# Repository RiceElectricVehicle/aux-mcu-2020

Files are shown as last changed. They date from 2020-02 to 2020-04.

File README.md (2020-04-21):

# Central Controller Code

Initial Author: Boyuan Deng

## Overview

This library is built for Rice Electric Vehicle Electric Team's auxilary board (aux board). The main function of the auxilary board include the following:

1. Take in and respond to information from pedal and break
2. Communicate with and respond to motor controller
3. Enable lighting control through switches installed on board
4. Display the car's status on screen

All the functions mentioned above requires the microcontroller on aux board. We've chosen Teensy 3.5 as the microcontroller, and the language for it is Arduino language, which is essentially C++ with Arduino's special libraries. We chose Serial Peripheral Interface (SPI) as the protocol between the aux board and the motor controller board. The following sections will detail the libraries and files contained in the library.

## External Libraries

Besides main.cpp, there are two external libraries under the /lib directory. You can add additional directories to /lib. Refer to the README under /lib to find out how to do that.

### Arduino-PID-Library-master

The Proportioal-Integral-Derivative (PID) control is a control loop mechanism used widely in industry. If you are unfamiliar with this, be sure to do some online research to understand it. The basic idea is to read a sensor, then compute the desired actuator output by calculating proportional, integral, and derivative responses and summing those three components to compute the output.

This library is an external libarary provided by Arduino. It is currently unused as the PID functionality has been taken care of by the motor controller. However, it still comes handy if you ever want PID in aux board. The constructor of the class is as below:
```
PID(double* Input, double* Output, double* Setpoint, double Kp, double Ki,
         double Kd, int POn, int ControllerDirection)
```
The PID input will be stored in first pointer, and the output second pointer, the setpoint third pointer. Three constants Kp, Ki and Kd are also required. You can specify the direction by last variable. A typical initialization of a PID object would look like below:
```
double pid_inA, pid_outA, pid_setA;
PID pidA(&pid_inA, &pid_outA, &pid_setA, 1, 1, 0, REVERSE);
```
Then in the main loop, you call
```
pidA.Compute();
```
And then `pid_outA` will contain desired output.

### OLED

This is a library that I personally write to drive the OLED screen. **Please install U8g2 in PlatformIO/your preferred IDE before it will work!** It is dependent on U8g2 libarary. A typical initialization would look like this:
```
OLED OLED_screen;
```
Internally a U8g2 screen object of the required type will be initialized. Then in your setup() routine, initializa the object by passing in a pointer to a location where the speed/power/whatever you want to show is stored:
```
OLED_screen.init(&speed);
```
After that, you can call it's functions like `display_braking`, `display_speed` etc. Some functions inside it is outdated, and you can add or replace some of them if you want.

## Main Code

Under /src directory are main control algorithms for the car.

### pins.h

Here we define necessary pins for main.cpp to use. In this way, we no longer need to memorize the pins for each functionality after we settled the design. You can find a pinout for Teensy 3.5 here:

https://www.pjrc.com/teensy/card8a_rev2.pdf

### main.cpp

This is the main control algorithm for aux board. I will explain some important variables I declared before I move to the algorithm itself.

##### Data

In SPI communication, we are transmitting 16 bits of information in forms of an integer. Manipulating this integer is a little trouble some, and `Data` is more easy to play with. `create_data()`, `decode_data()`, `encode_data()` and `print_data()` are self-explanatory helper functions to aid transition between struct and int.

##### Message ints

```
volatile unsigned int message_A_out;
volatile unsigned int message_A_in = 0;
volatile unsigned int message_B_out;
volatile unsigned int message_B_in = 0;
```
These are the variables we use to receive and send information over SPI. Rules for their encoding is explained in next section.

##### brk, direction and error

These are global variables keeping track of current state of the car.

##### The IntervalTimer objects

```
IntervalTimer clock_timer;
IntervalTimer SPI_timer;
```
These two IntervalTimer objects utilizes Teensy 3.5's hardware timed interrupts. They send out interrupt signals every certain amount of time, so that the designated function will execute every fixed amount of time. Meanwhile, main loop will pause.

#### The setup() routine

Here a few things need to be set up:

1. Set pinMode for necessary pins
2. Serial monitor, enabling debugging
3. Interrupt for break, as well we the IntervalTimer objects
4. SPI communication
5. OLED screen object

Refer to the code comments for implementation details.

#### The loop() routine

Currently useless. Important routines are wrapped inside IntervalTimer objects so they can be steadily and predicably executed every certain amount of time. However, potentially it can be used to monitor motor controller's state and react to it accordingly.

#### The blink() routine

This function send out signals to toggle headlight every half a second, so that it blinks.

#### The brake_isr() routine

Whenever there is a change in the `BRAKE_SNS` pin, this function will be executed. If it is activated when the current state is breaking, that means the brake is released. Otherwise, it means that the brake is been activated, then the current state is changed and we communicate with motor controller this change.

#### The get_and_send() routine

The core routine of main.cpp. First we read in values indicating position of the pedal. We then send this information along with current state over to motor controller. Note that you need to pull the pins low before you transmit the information, and pull the pins high after you finished.

## SPI specification

The information we send over in SPI is an 16-bit integer.

### 4 Most Significant Bits

4MSBs indicat the current state of the car. 1st bit indicate brake, 2nd bit direction, 3rd bit error, 4th bit currently left empty and for future use. For brake and error, 1 indicate "have" while 0 indicate "do not have" (e.g. 1 in brake indicate braking). For direction, 1 is forward while 0 is backward.

### 12 lower bits

12 lower bits are for set points. This allows for a resolution of 1/4096 for set points. The actual representation of the set points are by no means fixed, and feel free to change if you see fit.

### To conclude:

Brake|Direction|Error|Blank|12 bits of set point

#### Exersise:

What does 1100000000001111 mean?

Answer: Braking, forward, no errors and a setpoint of 31.

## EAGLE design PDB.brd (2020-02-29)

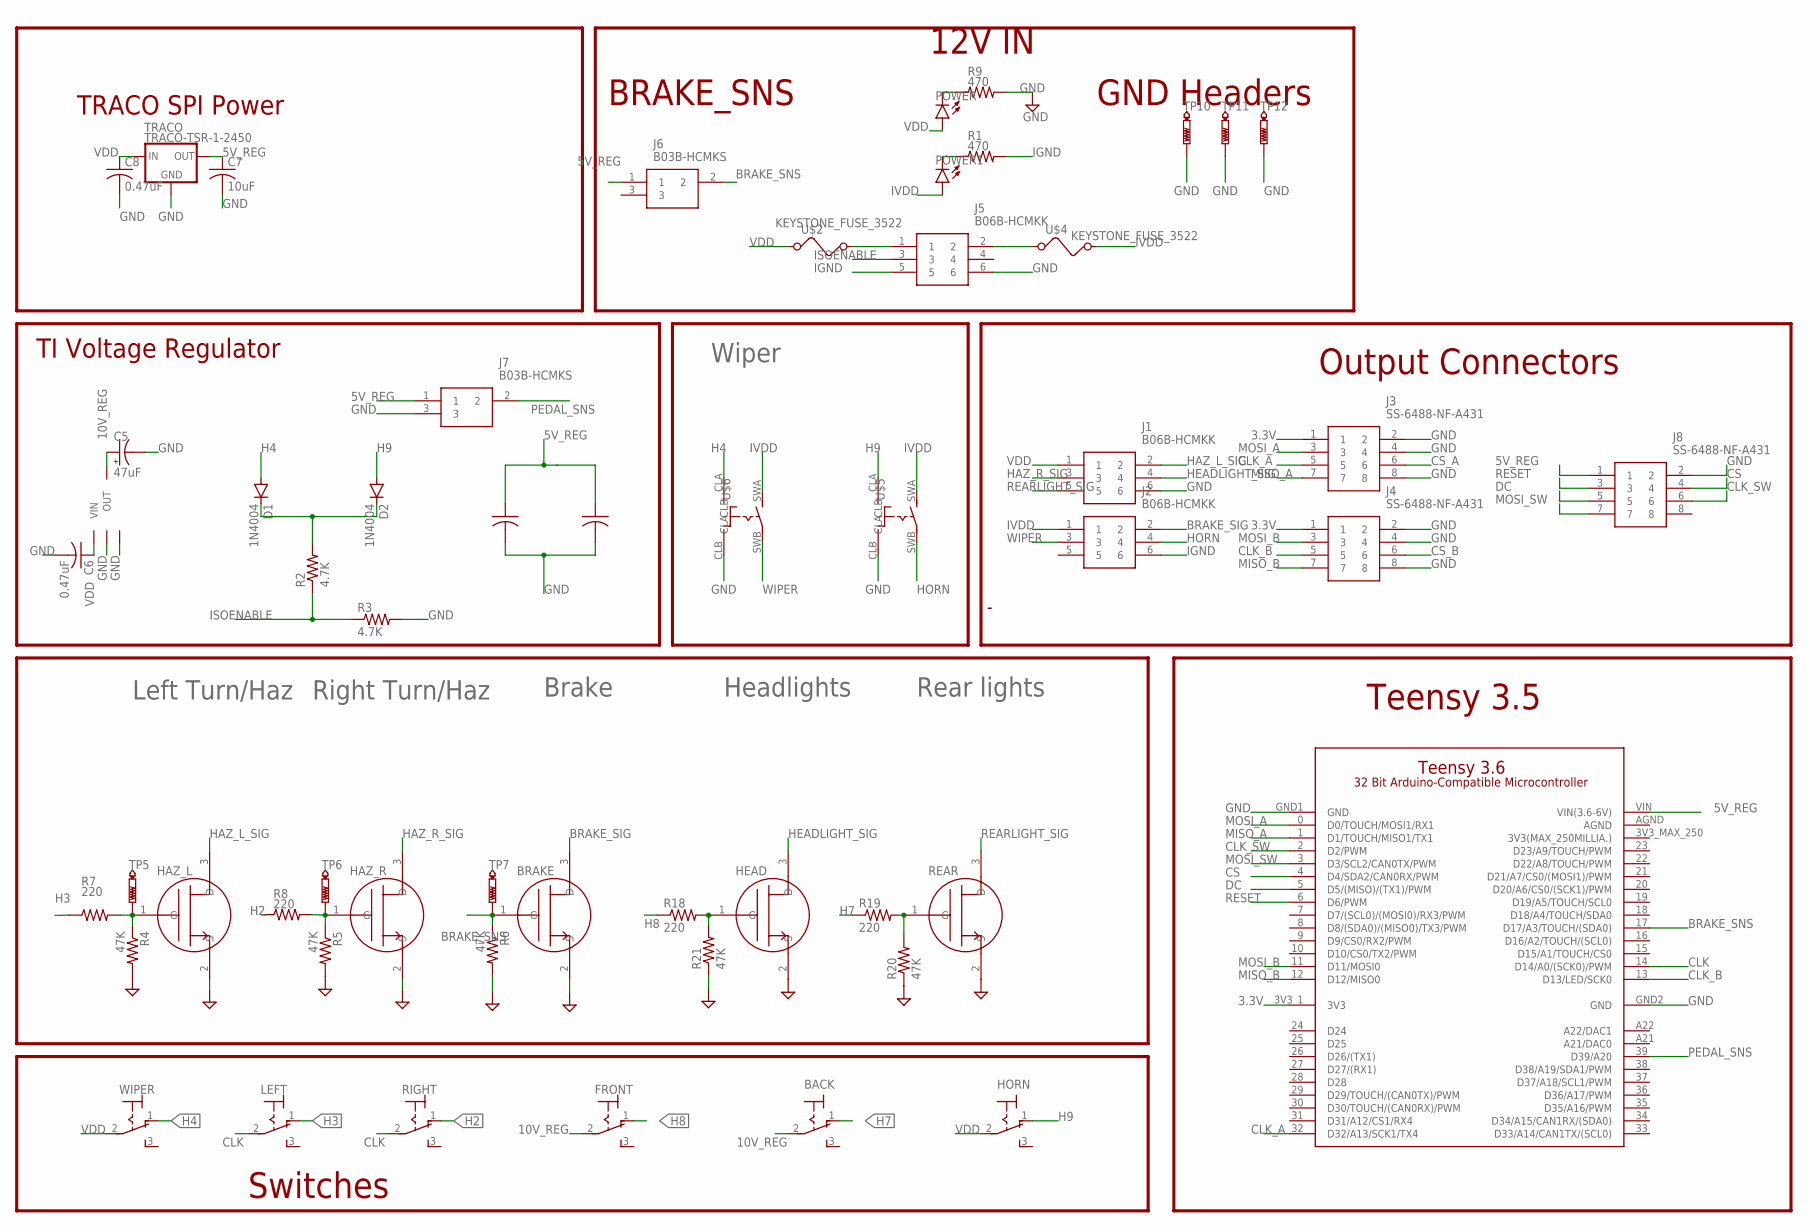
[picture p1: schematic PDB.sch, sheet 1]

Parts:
BACK: M9040P
BRAKE: NCV8405ADPAK-3PIN; TO254P1054X240-3
C1: 0.1uF; C0805
C2, C7: 10uF; C0805
C5: 47uF; PANASONIC_C
C6, C8: 0.47uF; C0805
D1, D2: 1N4004; DO41-10
FRONT: M9040P
HAZ_L: NCV8405ADPAK-3PIN; TO254P1054X240-3
HAZ_R: NCV8405ADPAK-3PIN; TO254P1054X240-3
HEAD: NCV8405ADPAK-3PIN; TO254P1054X240-3
HORN: M9040P
J1, J2, J5: B06B-HCMKK; B06BHCMKK
J3, J4, J8: SS-6488-NF-A431; SS6488NFA431
J6, J7: B03B-HCMKS; B03BHCMKS
LEFT: M9040P
LM2940: LM2940LM; SOT230P700X180-4
POWER, POWER1: LEDCHIPLED_0805; CHIPLED_0805
R1, R9: 470; R3225
R2, R3: 4.7K; R0805
R4, R5, R6, R20, R21: 47K; R0805
R7, R8, R18, R19: 220; R0805
REAR: NCV8405ADPAK-3PIN; TO254P1054X240-3
RIGHT: M9040P
TP5, TP6, TP7: PTR1B2,54; B2,54
TP10, TP11, TP12: PTR1PAD1-13Y; P1-13Y
TRACO: TRACO-TSR-1-2450; SIP3
U$2, U$4: KEYSTONE_FUSE_3522
U$3: TEENSY-3.6_ONLY_HOLES
U$5, U$6: TE_CON_OJE-SH-112DM,095\; TE_CON_OJE-SH-112DM,095
WIPER: M9040P

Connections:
3.3V: J3.1, J4.1, U$3.3V3_1 (3V3)
5V_REG: C1.1, C2.1, C7.1, J6.1, J7.1, J8.1, TRACO.3 (OUT), U$3.VIN (VIN(3.6-6V))
10V_REG: BACK.2, C5.+, FRONT.2, LM2940.3 (OUT)
AGND: U$3.AGND
BRAKE_SIG: BRAKE.3 (D), J2.2
BRAKE_SNS: BRAKE.1 (G), J6.2, R6.1, TP7.TP, U$3.17 (D17/A3/TOUCH/(SDA0))
CLK: LEFT.2, RIGHT.2, U$3.14 (D14/A0/(SCK0)/PWM)
CLK_A: J3.5, U$3.32 (D32/A13/SCK1/TX4)
CLK_B: J4.5, U$3.13 (D13/LED/SCK0)
CLK_SW: J8.6, U$3.2 (D2/PWM)
CS: J8.4, U$3.4 (D4/SDA2/CAN0RX/PWM)
CS_A: J3.6
CS_B: J4.6
DC: J8.5, U$3.5 (D5/(MISO)/(TX1)/PWM)
GND: BRAKE.2 (S), C1.2, C2.2, C5.-, C6.2, C7.2, C8.2, HAZ_L.2 (S), HAZ_R.2 (S), HEAD.2 (S), J1.6, J3.2, J3.4, J3.8, J4.2, J4.4, J4.8, J5.6, J7.3, J8.2, LM2940.2 (GND2), LM2940.4 (GND), R3.2, R4.2, R5.2, R6.2, R9.2, R20.1, R21.1, REAR.2 (S), TP10.TP, TP11.TP, TP12.TP, TRACO.2 (GND), U$3.GND1 (GND), U$3.GND2 (GND), U$5.CLB, U$6.CLB
H2: R8.1, RIGHT.1 (O)
H3: LEFT.1 (O), R7.1
H4: D1.A, U$6.CLA, WIPER.1 (O)
H7: BACK.1 (O), R19.1
H8: FRONT.1 (O), R18.1
H9: D2.A, HORN.1 (O), U$5.CLA
HAZ_L_SIG: HAZ_L.3 (D), J1.2
HAZ_R_SIG: HAZ_R.3 (D), J1.3
HEADLIGHT_SIG: HEAD.3 (D), J1.4
HL_GATE: HAZ_L.1 (G), R4.1, R7.2, TP5.TP
HORN: J2.4, U$5.SWB
HR_GATE: HAZ_R.1 (G), R5.1, R8.2, TP6.TP
IGND: J2.6, J5.5, R1.2
ISOENABLE: J5.3, R2.1, R3.1
IVDD: J2.1, POWER1.A, U$4.B1 (2), U$4.B2 (2), U$5.SWA, U$6.SWA
MISO_A: J3.7, U$3.1 (D1/TOUCH/MISO1/TX1)
MISO_B: J4.7, U$3.12 (D12/MISO0)
MOSI_A: J3.3, U$3.0 (D0/TOUCH/MOSI1/RX1)
MOSI_B: J4.3, U$3.11 (D11/MOSI0)
MOSI_SW: J8.7, U$3.3 (D3/SCL2/CAN0TX/PWM)
unnamed: POWER.C, R9.1
unnamed: D1.C, D2.C, R2.2
unnamed: J5.1, U$2.B1 (2), U$2.B2 (2)
unnamed: J5.2, U$4.A1 (1), U$4.A2 (1)
unnamed: POWER1.C, R1.1
unnamed: HEAD.1 (G), R18.2, R21.2
unnamed: R19.2, R20.2, REAR.1 (G)
PEDAL_SNS: J7.2, U$3.39 (D39/A20)
REARLIGHT_SIG: J1.5, REAR.3 (D)
RESET: J8.3, U$3.6 (D6/PWM)
VDD: C6.1, C8.1, HORN.2, J1.1, LM2940.1 (VIN), POWER.A, TRACO.1 (IN), U$2.A1 (1), U$2.A2 (1), WIPER.2
WIPER: J2.3, U$6.SWB

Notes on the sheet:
12V IN
BRAKE_SNS
Switches
Wiper
Left Turn/Haz
Right Turn/Haz
Brake
Headlights
Rear lights
GND Headers
Output Connectors
TRACO SPI Power
TI Voltage Regulator
Teensy 3.5

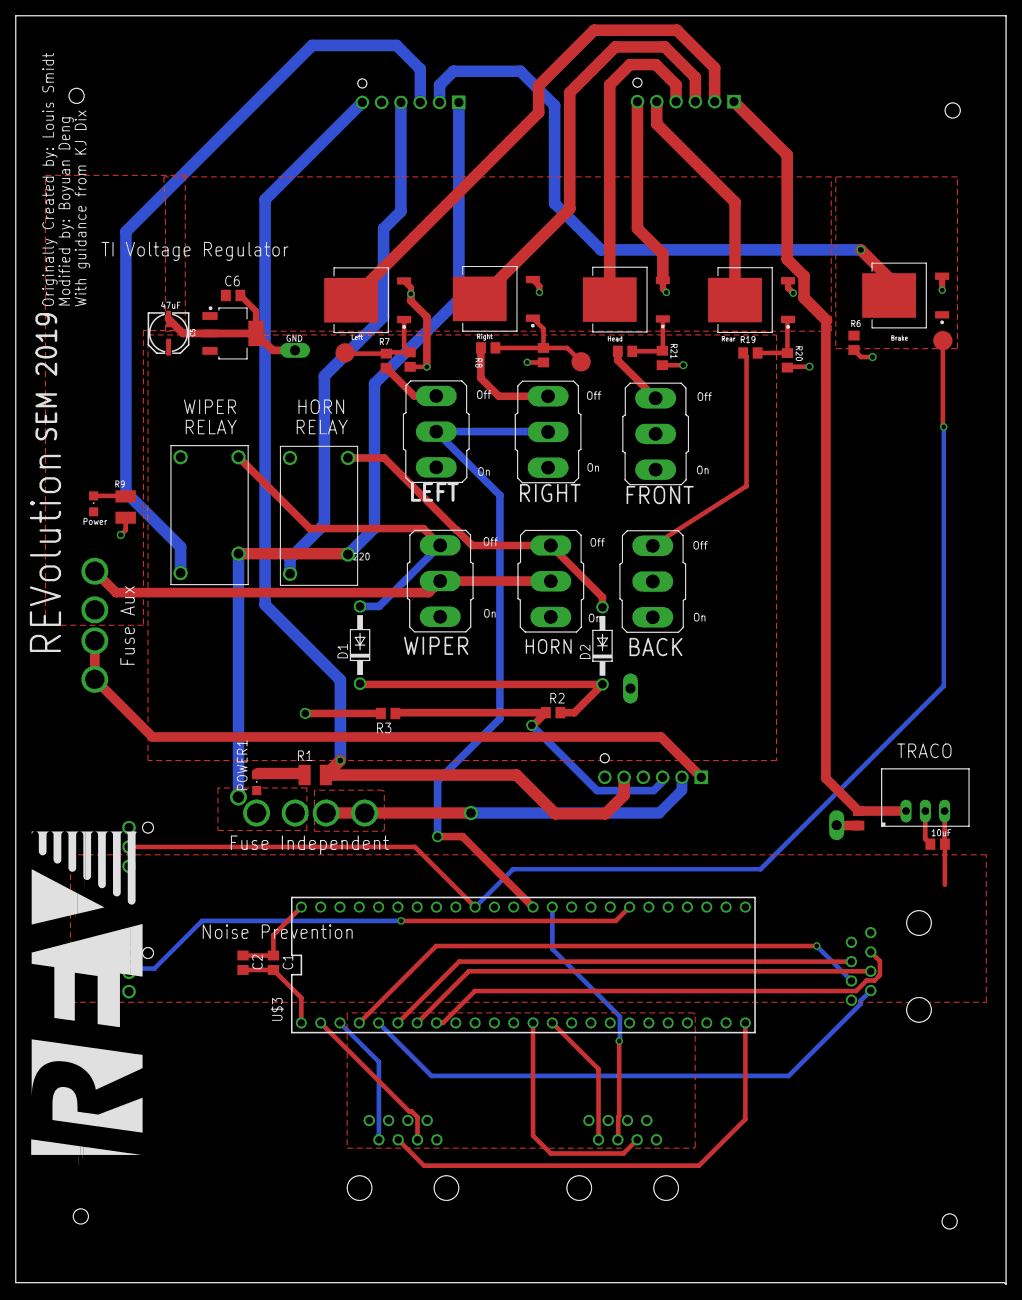
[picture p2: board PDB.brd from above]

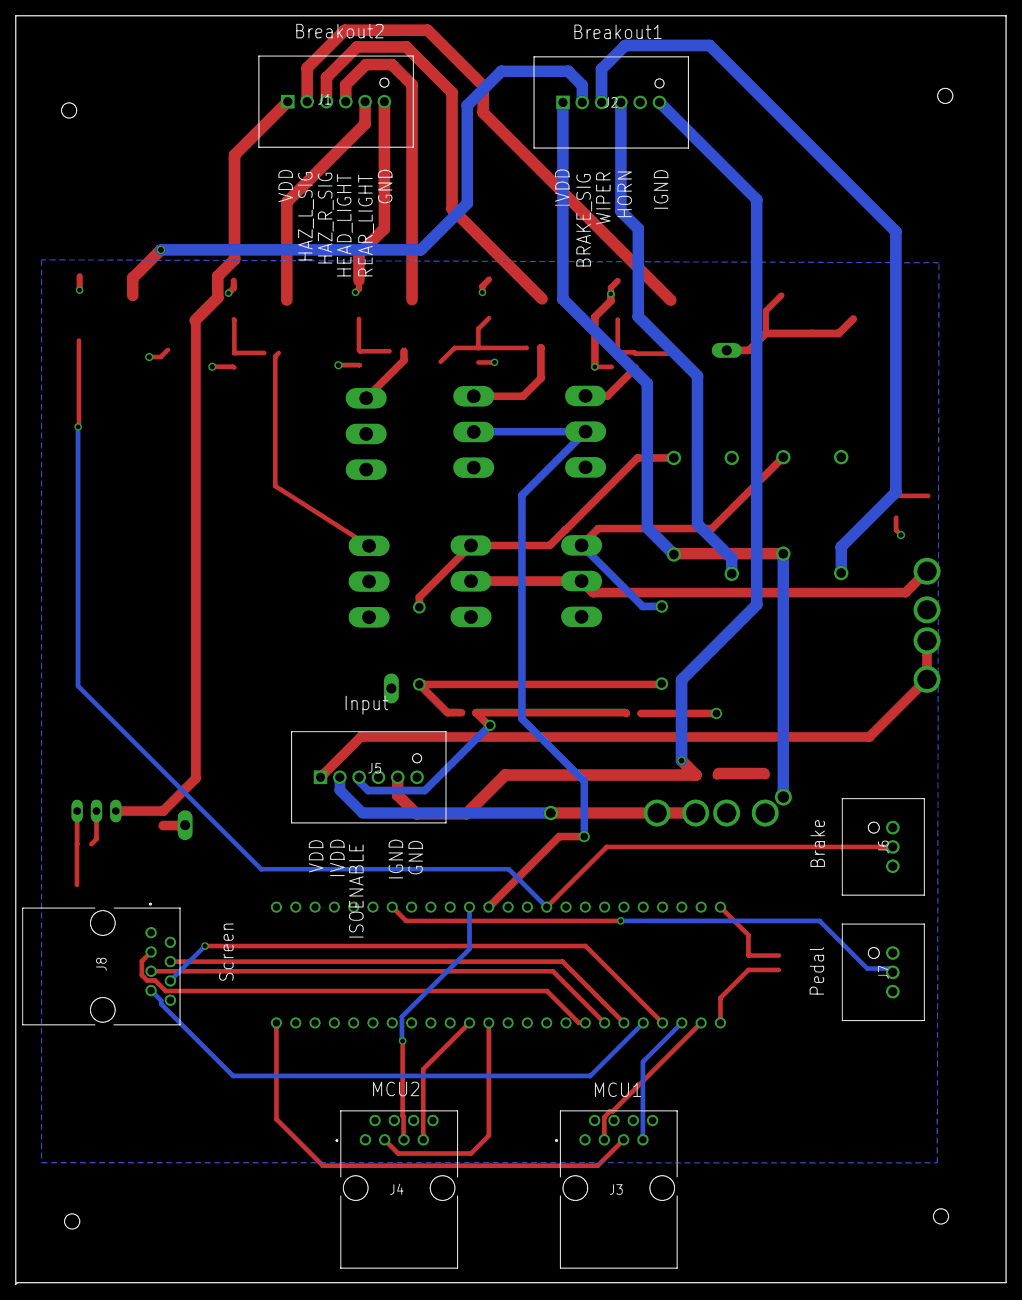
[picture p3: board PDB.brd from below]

Board: 2 copper layers, 130.3 x 166.9 mm, 55 parts (8 on the bottom side), 44 nets.

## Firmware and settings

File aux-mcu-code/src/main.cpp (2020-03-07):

#include <Arduino.h>
#include <avr/interrupt.h>
#include <avr/io.h>
#include <OLED.h>
#include <PID_v1.h>
#include <pins.h>
#include <SPI.h>

// Clearing confusion in dirction
#define FORWARD true;
#define BACKWARD false;

typedef struct Data {
  // Setpoint or currentpoint
  unsigned int point;
  // Brake
  bool brake;
  // Direction, true forward and false backward
  bool direction;
  // Error
  bool error;
} Data;

OLED OLED_screen;
volatile double speed;

/**
* Rules for messages below:
* 4MSB is for operands, 12 lower bits are for setpoints
* 4MSB are arranged as below: Brake, Direction, Error, Empty
*/
volatile unsigned int message_A_out;
volatile unsigned int message_A_in = 0;
volatile unsigned int message_B_out;
volatile unsigned int message_B_in = 0;

// Record of break state
volatile bool brk = false;

volatile bool direction = FORWARD;

volatile bool error = false;

volatile bool error_A;
volatile bool error_B;

// Pedal sensing
volatile int pedal_adc;
volatile double pedal_power;

// PID loops
// double pid_inA, pid_outA, pid_setA;
// double pid_inB, pid_outB, pid_setB;
// PID pidA(&pid_inA, &pid_outA, &pid_setA, 1, 1, 0, REVERSE);
// PID pidB(&pid_inB, &pid_outB, &pid_setB, 1, 1, 0, REVERSE);

// The timer to switch on and off
IntervalTimer clock_timer;

IntervalTimer SPI_timer;

// Record for blinking the lights
int light_state = HIGH;

// For testing usage
const bool testing = true;

void blink();
// void pidSetup();
void brake_isr();
void get_and_send();
Data create_data(unsigned int point, bool brake, bool direction, bool error);
Data decode_data(unsigned int message);
unsigned int encode_data(Data current_data);
void print_data(const char* message, Data data);

void setup() {
  // Set pinmode
  pinMode(CLK, OUTPUT);
  pinMode(SS_A, OUTPUT);
  pinMode(SS_B, OUTPUT);

  // Begin transimitting to serial
  Serial.begin(9600);
  Serial.println("Starting");

  // disable interrupts
  cli();
  // attachInterrupt(FAULT_IN, fault_catch, CHANGE);
  attachInterrupt(BRAKE_SNS, brake_isr, CHANGE);
  SPI_timer.begin(get_and_send, 250000);
  // enable interrups
  sei();

  // Start timer
  clock_timer.begin(blink, 500000);
  clock_timer.priority(200);

  // Start the SPI
  SPI.begin();
  SPI1.begin();

  // Start PID setup
  // pidSetup();

  // Set up OLED screen
  OLED_screen.init(&speed);
}

void loop() {
  Data from_A = decode_data(message_A_in);
  Data from_B = decode_data(message_B_in);
  error_A = from_A.error;
  error_B = from_B.error;
  error = error_A || error_B;
  if (testing)
  {
    print_data("Motor A -------", from_A);
    print_data("Motor B -------", from_B);
  }
  delay(100);
}

/**
 * Blink the headlights
 */
void blink()
{
  // Serial.println("Blinking");
  digitalWrite(CLK, light_state);
  if (light_state == HIGH)
  {
    light_state = LOW;
  } else
  {
    light_state = HIGH;
  }
  // Serial.println(light_state);
}

// void pidSetup() {
//   pidA.SetOutputLimits(0, 4096);
//   pidB.SetOutputLimits(0, 4096);
//   pidA.SetMode(AUTOMATIC);
//   pidB.SetMode(AUTOMATIC);
//   Serial.println("Setup done");
// }

/**
 * If brake change is detected, let it be false
 */
void brake_isr() {
  cli();
  if (brk)
  {
    brk = false;
    sei();
  }
  else
  {
    brk = true;
    message_A_out = 1 << 15;
    message_B_out = 1 << 15;
    digitalWrite(SS_A, LOW);
    digitalWrite(SS_B, LOW);
    message_A_in = SPI.transfer16(message_A_out);
    message_B_in = SPI1.transfer16(message_B_out);
    digitalWrite(SS_A, HIGH);
    digitalWrite(SS_B, HIGH);
    sei();
  }
}

void get_and_send()
{
        if (testing)
        {
          pedal_power = 3000;
          direction = BACKWARD;
          Serial.println("Sending data --------------------------");
        }
        else
        {
          pedal_adc = analogRead(PEDAL_SNS);
          pedal_power = map(pedal_adc, 550, 900, 0, 4095);
        }
        cli();
        Data send_A = create_data(pedal_power, brk, direction, error);
        Data send_B = create_data(pedal_power, brk, direction, error);
        message_A_out = encode_data(send_A);
        message_B_out = encode_data(send_B);
        // if (testing)
        // {
        //   print_data("Sending A -------", send_A);
        //   print_data("Sending B -------", send_B);
        // }
        digitalWrite(SS_A, LOW);
        digitalWrite(SS_B, LOW);
        message_A_in = SPI.transfer16(message_A_out);
        message_B_in = SPI1.transfer16(message_B_out);
        digitalWrite(SS_A, HIGH);
        digitalWrite(SS_B, HIGH);
        sei();
}

/**
 * Create a "Data" structure with information needed
 */
Data create_data(unsigned int point, bool brake, bool direction, bool error)
{
  Data current_data;
  current_data.point = point;
  current_data.brake = brake;
  current_data.direction = direction;
  current_data.error = error;

  return current_data;
}

/**
 * Take in a encoded int, decode it as "Data" structure
 */
Data decode_data(unsigned int message)
{
  unsigned int point = message & 0xFFF; // Take 12 LSB
  bool brake = message >> 15; // Take MSB
  bool direction = (message >> 14) & 1; // Take 2nd MSB
  bool error = (message >> 13) & 1; // Take 3rd MSB
  Data current_data = create_data(point, brake, direction, error);
  return current_data;
}

/**
 * Take in a "Data" structure, encode it as a int
 */
unsigned int encode_data(Data current_data)
{
  // Set the point
  unsigned int message = current_data.point & 0xFFF;

  // Set the brake
  if (current_data.brake)
  {
    message |= (1 << 15);
  }

  // Set the direction
  if (current_data.direction)
  {
    message |= (1 << 14);
  }

  // Set the error
  if (current_data.error)
  {
    message |= (1 << 13);
  }

  return message;
}

void print_data(const char* message, Data data)
{
  Serial.println(message);
  Serial.print("Set point: ");
  Serial.println(data.point);
  Serial.print("Brake: ");
  Serial.println(data.brake ? "true" : "false");
  Serial.print("Direction: ");
  Serial.println(data.direction ? "forward" : "backward");
  Serial.print("Error: ");
  Serial.println(data.error ? "true" : "false");
}

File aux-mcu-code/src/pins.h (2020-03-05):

#ifndef PINS_H
#define PINS_H

// Motor controller A
#define MOSI_A 0
#define MISO_A 1
#define SS_A 31
#define CLK_A 32

// Motor controller B
#define MOSI_B 11
#define MISO_B 12
#define SS_B 15
#define CLK_B 13

// Screen SPI
#define MOSI_SW 3
#define CS 4
#define DC 5
#define RESET 6
#define CLK_SW 2

// Clock signal
#define CLK 14

// Pedal
#define PEDAL_SNS 39

// Brake
#define BRAKE_SNS 17

#endif  // PINS_H

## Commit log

2019-10-19 Aux board from last year
    [PDB.brd, PDB.sch]
2019-10-26 Deleted SPI, ADD2
    [PDB.brd, PDB.sch]
2019-10-26 Changed GND to VDD for connector
    [PDB.brd, PDB.sch]
2019-10-28 Disconnected 555-timer from the jumper
    [PDB.brd, PDB.sch]
2019-10-28 Deleted Anderson connector for left and right light
    [PDB.brd, PDB.sch]
2019-10-28 Last time forget to save. This is the real version of last commit.
    [PDB.brd, PDB.sch]
2019-10-29 Deleted most Anderson connectors. Brake sensor waiting to be modified
    [PDB.brd, PDB.sch]
2019-10-30 adds new connectors and relays, and removes old connectors and wiper fet
    [PDB.brd, PDB.sch]
2019-11-01 added master library to repository
    [PDB.sch]
2019-11-01 Schemetic first draft done
    [PDB.brd, PDB.sch]
2019-11-01 Schematic first version
    [PDB.brd, PDB.sch]
2019-11-01 Board layout proposal
    [PDB.brd, PDB.sch]
2019-11-02 Board first version
    [PDB.brd, PDB.sch]
2019-11-02 Decorative modification
    [PDB.brd]
2019-11-02 VIPER misspelling corrected
    [PDB.brd, PDB.sch]
2019-11-05 Widen the traces of independent 12V and indipendent ground
    [PDB.brd, PDB.sch]
2019-11-07 Added voltage divider so that Teensy 3.5 sees Wiper and Horn are turned on
    [PDB.brd, PDB.sch]
2019-11-12 With diode, pass signal direcely to ISOENABLE
    [PDB.brd, PDB.sch]
2019-11-19 Flipped all connectors to the back side, added capacitors connecting Teensy's 5V_REG to GND
    [PDB.brd, PDB.sch]
2019-11-19 Silkscreen finished.
    [PDB.brd]
2019-11-19 slightly moved traces that were close
    [PDB.brd]
2019-11-19 Adjusted schematic and routing to pass twisted pairs to each signal
    [PDB.brd, PDB.sch]
2019-11-23 switched order of output bus
    [PDB.brd]
2019-11-24 Edited skilscreen to fit new connector arrangement, reversed ethernet cable to screen to correct direction.
    [PDB.brd]
2020-01-25 Code folder added.
    [PDB.brd, PDB.sch]
2020-01-25 Changed OLED folder modified for software SPI.
2020-02-04 Set up the PID.
2020-02-27 adds cs signal but does not route it
    [PDB.brd, PDB.sch]
2020-03-05 Debugged SPI.
2020-03-07 Changed SPI from loop to interrupts.

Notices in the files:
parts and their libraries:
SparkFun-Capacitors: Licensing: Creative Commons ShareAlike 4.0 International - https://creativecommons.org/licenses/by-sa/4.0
